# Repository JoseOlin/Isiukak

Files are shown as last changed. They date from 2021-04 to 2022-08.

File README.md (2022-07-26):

# Sistema de Conducción Isiukak

Código, piezas 3D, diagramas y esquemáticos y  para replicar el **sistema Isiukak para conducción con Joystick**.

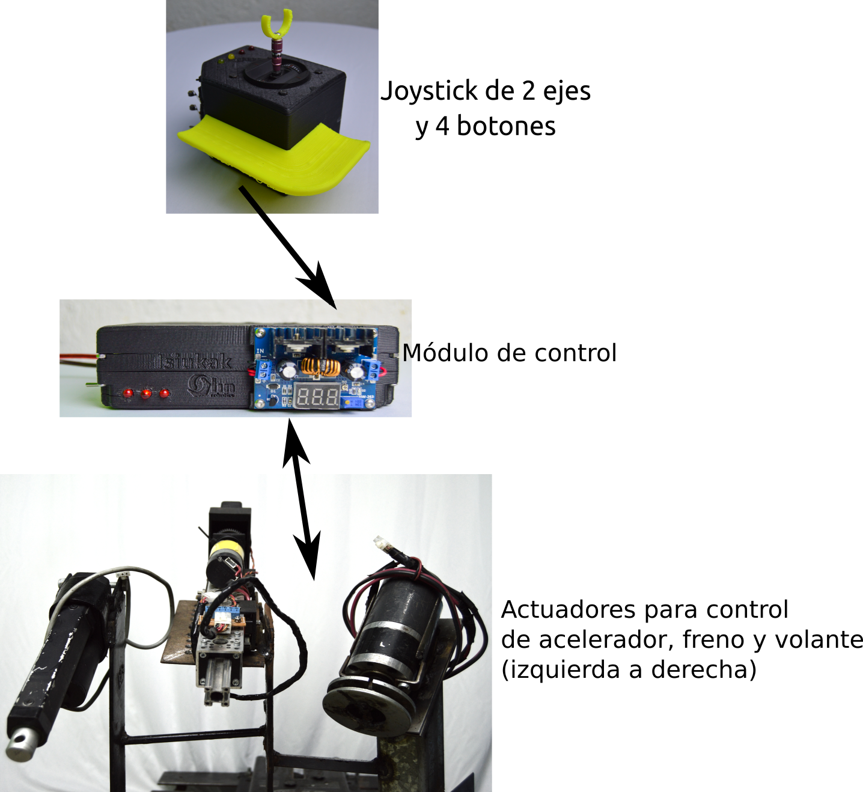
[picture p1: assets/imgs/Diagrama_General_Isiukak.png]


La carpeta **Programas** contiene dos carpetas. 
- **Arduino_PlatformIO** contiene el código en lenguaje Arduino para el microcontrolador del módulo de control. 
- **MonitorSerial_Qt** es un programa en C++/Qt para monitorear los valores del sistema en tiempo real.

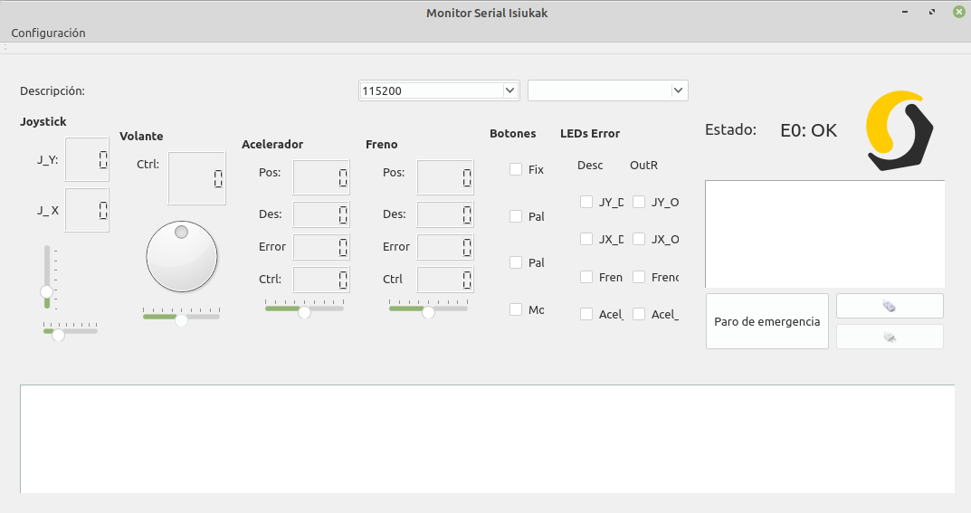
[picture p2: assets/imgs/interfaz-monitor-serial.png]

Más detalles en el [archivo README.md de la carpeta Programas](Programas/README.md)

La carpeta **Componentes_3DParts_Schematics** contiene el diagrama general del sistema y los esquemáticos de cada subsistema, así como las piezas 3D necesarias y fotografías de las piezas construidas.

Si requieres más información acerca de los componentes del sistema puedes visitar la [página del proyecto Isiukak en Olin Robotics](https://www.olinrobotics.com/proyecto_isiukak)

# Estructura general del sistema

Los subsistemas del Isiukak son:

- Módulo de control

- Joystick

- Actuación de pedales, volante y palanca

Que se muestran a continuación.



El **módulo de control** es la parte central, donde se realiza el procesamiento del sistema. Lee la  posición del *joystick* para controlar los pedales y el volante. 

El **eje vertical del joystick, controla el freno y el acelerador**, mientras que el **eje horizontal asiste en el movimiento del volante**. La palanca de cambios se  controla con dos botones ubicados en el mismo joystick.

Dos actuadores lineales controlan el freno y el acelerador, un tercer motor asiste en el movimiento del volante y otro actuador lineal asiste en el movimiento de la palanca.

Actualmente se tiene una prueba de concepto del sistema implementada en un Arduino UNO. La siguiente etapa portar el código a un microcontrolador de grado automotriz.

# Acerca del Software
Utilizamos [PlatformIO](https://platformio.org/) para la compilación del código en Arduino, con [Qt Creator](https://www.qt.io/product/development-tools) como editor.
 
El software se comparte con la mejor intención de que como comunidad desarrollemos tecnología de asistencia que nos permita una vida más autónoma, pero sin garantías. **Úsalo bajo tu propia responsabilidad**.

 Esperamos que te diviertas tanto como nosotros desarrollándolo. Que la Autonomía te acompañe.

## Versionado Semántico
Estamos en proceso de adoptar [versionado semántico (SemVer)](https://semver.org/) para la nomenclatura de las versiones liberadas.

Dada un número de versión MAYOR.MENOR.PATCH, se incrementa:
1. MAYOR cuando se hace un **cambio incompatible a la API**.
2. MENOR cuando se agrega funcionalidad compatible con versiones anteriores.
3. PATCH cuando se arreglan bugs compatibles con versiones anteriores.

Una versión MAYOR **0 indica que se está en las primeras etapas de desarrollo**, la API es inestable y puede tener muchos cambios.

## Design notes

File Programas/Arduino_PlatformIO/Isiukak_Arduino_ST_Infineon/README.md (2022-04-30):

# Sistema Conducción Joystick

El archivo principal es  **ControlActuadoresJoystick_Retro.cpp**

## Joystick

```
        ^
        |
        |
  <----------->  JyHor
        |
        |
        JyVer
```

### LEDs

| | L1 | L2 | L3 | L4 |
| ----- | --- | --- | --- | --- |
| Blkng | JyNoCentro | PotsDscn  | ActFueraRango | ActsNoMov  |
| Stdy  | AcelDscn | JyHorDscn | FrenoDscn | JyVerDescn |

## Botones

FijarPosiciónFreno

SubirPalanca

BajarPalanca

ModoCarretera

# Referencia de pines
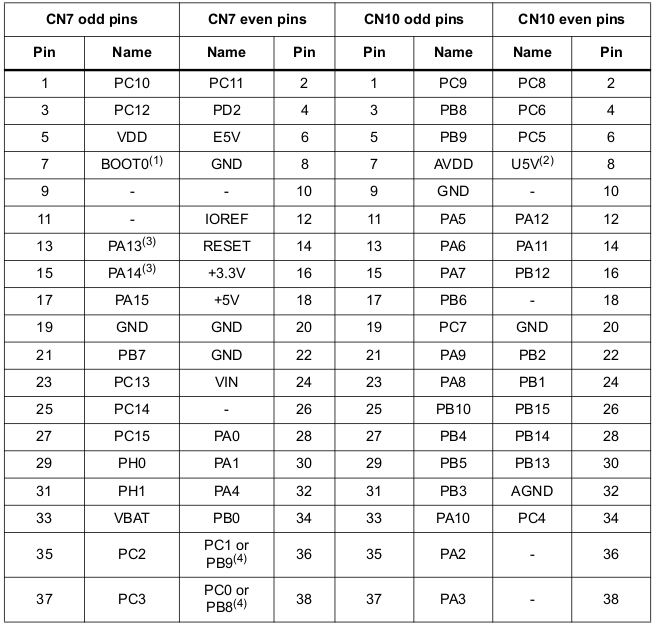
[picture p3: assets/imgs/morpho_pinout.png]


## Pines analógicos:

**A0: INPUT Analógica**. Joystick eje Y. Incremento acelera, decremento frena.

**A1: INPUT Analógica**. Josytick eje X. (Volante).

**A2: INPUT Analógica**. Pot actuador 1. (Freno).

**A3: INPUT Analógica**. Pot actuador 2. (Accel).

**A4: INPUT Digital.** (Future) J_Y second pot

**A5: INPUT Digital.** (Future) J_X second pot

En el ST NUCLEO la referencia para el ADC debe configurarse AVDD = VDDVirtual, AGND = GNDVirtual 

## Pines digitales:

### Comunicación serial con el Monitor
**0 (PA3):** Serial Rx

**1 (PA2):** Serial Tx

### Comunicación serial con los puentes
**2 (PA10): INPUT.**  **smcSerial RX**. Hacia los Drivers de los motores.

**8 (PA9): OUTPUT**. **smcSerial TX**. Hacia los Drivers de los motores.  

### Voltaje digital para corroborar conexión de potenciómetros
**3: OUTPUT**. **5V Virtual**. Para Validación de potenciómetros conectados.

**7: OUTPUT.** **GND Virtual**.

### Pines de control de la palanca
**4: OUTPUT. pinPalanca_Bajar.** Pin para controlar el puente H de la palanca.

**5: OUTPUT. pinPalanca_Bajar.** Pin para controlar el puebte H de la palanca.

### Botones y switches
**10: INPUT.** Botón Bajar Palanca.

**11: INPUT.** Switch Modo Carretera.

### Voltaje de referencia para el ADC.
**12: OUTPUT.** V_SSA Voltaje referencia ADC GND.

**13: OUTPUT**: V_DDA Volt referencia ADC VDD.

### Otros
**6**: **Not used** 

**9: INPUT_PULLUP. PinParoManualEmergencia.**

# Operation Modes

The Isiukak have 3 modes of operation.
- **Normal mode**: Read the joystick and control the actuators.
- **Embedded Testing**: Set predefined values for the joystick and the flags of connection and normal range of the pots to check if the safety routines works properly.
- **Joystick Virtual**: Pending of implementation. This mode receives remote values for the joystick over Serial.

# Calibración del Sitema

## Actuadores

Actualizar las siguientes variables:

actFreno_valorExtendido
actFreno_valorRetraido
actFreno_valorParoEmergencia

actAcel_valorExtendido
actAcel_valorRetraido

# Configurar QtCreator para compilar código de Arduino con PlatformIO

Para facilitar el desarrollo en lugar de usar el IDE de Arduino se utiliza QtCreator con PlatformIO para compilar y editar el código.

Requiere instalación de Qt Creator y PlatformIO

pip3 install -U platformio

La sección **Projects** de Qt Creator debe configurarse de la siguiente forma.

## Build Settings

Edit build configuration: Debug

**Build directory:** El directorio donde esté **platform.ini**

**Buils Steps.** Borrar todos los items

Build steps → Custom Process Step.

- Command: `platformio`
- **Arguments**: `-f -c qtcreator run`
- **Working directory**: %{buildDir}

**Clean Steps.** ``Borrar todos los items
Add clean step → Custom Process step

- **Command**: `platformio`
- **Arguments**: `-f -c qtcreator run --target clean`
- **Working directory**`: ``%{buildDir}`

## Deploy  Settings

Project → Run → Deploy configuration → Add Deploy Step → Custom Process Step
 • **Command:** platformio
 • **Arguments**: run --target upload
 • **Working directory**: %{buildDir}

# Release Notes

## 0.9.1

En esta versión el actuador del freno puede tener retroalimentación con una resistencia variable (por ejemplo con los actuadores de Pololu o Servocity) o con un encoder (por ejemplo el actuador de GoBilda)

# Tareas futuras

**TODO**: Implementar lectura de status de los drivers DC para detectar sobretemperatura, etc. P2
**TODO**: Cambiar el orden de los pines para dejar el 2 para Serial y que sea compatible con ST NUCLEO.

# Standards a Considerar

## MISRA C

Motor Industry Software Reliability Association C Standard

## AUTOSAR

## NASA (Código)

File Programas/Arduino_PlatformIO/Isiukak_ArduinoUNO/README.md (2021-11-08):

# Sistema Conducción Joystick

El archivo principal es **ControlActuadoresJoystick_Retro.cpp**

## Joystick

```
        ^
        |
        |
  <----------->  JyHor
        |
        |
        JyVer
```

### LEDs

| | L1 | L2 | L3 | L4 |
| ----- | --- | --- | --- | --- |
| Blkng | JyNoCentro | PotsDscn  | ActFueraRango | ActsNoMov  |
| Stdy  | AcelDscn | JyHorDscn | FrenoDscn | JyVerDescn |

## Botones

FijarPosiciónFreno

SubirPalanca

BajarPalanca

ModoCarretera

# Referencia de pines

## Pines analógicos:

**A0: INPUT Analógica**. Joystick eje Y. Incremento acelera, decremento frena.
**A1: INPUT Analógica**. Josytick eje X. (Volante).
**A2: INPUT Analógica**. Pot actuador 1. (Freno).
**A3: INPUT Analógica**. Pot actuador 2. (Accel).
**A4: INPUT Digital.** Botón Fijar Posición Freno
**A5: INPUT Digital.** Botón Subir Palanca.

## Pines digitales:

**15: I2C SDA**:  Conectado a A4 ó A5.
**14: I2C SCL**:  Conectado a A4 ó A5.
13: Pendiente de implementación
12: Pendiente de implementación
**11: INPUT.** Switch Modo Carretera.
**10: INPUT.** Botón Bajar Palanca.

**9: INPUT_PULLUP. PinParoManualEmergencia.**
**8: OUTPUT**. Tx Software serial. Hacia los Drivers de los motores.
**7: INPUT.** Rx Software Serial. Desde los Drivers de los motores.

6: INPUT. Implementar GND Virtual en este pin para liberar el 2 para comunicación del ST.
**5: OUTPUT. pinPalanca_Bajar.** Pin para controlar el puebte H de la palanca.
**4: OUTPUT. pinPalanca_Bajar.** Pin para controlar el puente H de la palanca.

**3: OUTPUT**. **5V Virtual**. Para Validación de potenciómetros conectados.
**2: OUTPUT**. **GND Virtual**. Para Validación de potenciómetros conectados

**1:** Serial Tx
**0:** Serial Rx

# Calibración del Sitema

## Actuadores

Actualizar las siguientes variables:

actFreno_valorExtendido
actFreno_valorRetraido
actFreno_valorParoEmergencia

actAcel_valorExtendido
actAcel_valorRetraido

# Configurar QtCreator para compilar código de Arduino con PlatformIO

Para facilitar el desarrollo en lugar de usar el IDE de Arduino se utiliza QtCreator con PlatformIO para compilar y editar el código.

Requiere instalación de Qt Creator y PlatformIO

pip3 install -U platformio

La sección **Projects** de Qt Creator debe configurarse de la siguiente forma.

## Build Settings

Edit build configuration: Debug

**Build directory:** El directorio donde esté **platform.ini**

**Buils Steps.** Borrar todos los items

Build steps → Custom Process Step.

- Command: `platformio`
- **Arguments**: `-f -c qtcreator run`
- **Working directory**: %{buildDir}

**Clean Steps.** ``Borrar todos los items
Add clean step → Custom Process step

- **Command**: `platformio`
- **Arguments**: `-f -c qtcreator run --target clean`
- **Working directory**`: ``%{buildDir}`

## Deploy  Settings

Project → Run → Deploy configuration → Add Deploy Step → Custom Process Step
 • **Command:** platformio
 • **Arguments**: run --target upload
 • **Working directory**: %{buildDir}

# Release Notes

## 0.9.1

En esta versión el actuador del freno puede tener retroalimentación con una resistencia variable (por ejemplo con los actuadores de Pololu o Servocity) o con un encoder (por ejemplo el actuador de GoBilda)

# Tareas futuras

**TODO**: Implementar lectura de status de los drivers DC para detectar sobretemperatura, etc. P2
**TODO**: Cambiar el orden de los pines para dejar el 2 para Serial y que sea compatible con ST NUCLEO.

# Standards a Considerar

## MISRA C

Motor Industry Software Reliability Association C Standard

## AUTOSAR

## NASA (Código)

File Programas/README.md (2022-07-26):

La carpeta **Arduino_(PlatformIO)** incluye el **código en lenguaje Arduino para el microcontrolador del módulo de control**. Se utiliza **PlatformIO** para compilar el código y **Qt Creator como IDE de desarrollo**.

La carpeta con el código más completo está en **Isiukak_Arduino_ST_Infineon**.

La carpeta **MonitorSerial_(Qt)** incluye el código para monitorear el sistema en tiempo real. La computadora donde se ejecute este programa (en nuestro caso una minilaptop) debe conectarse el módulo de control por USB. 

Imagen de la interfaz del monitor serie

# Instalar udev rules para tarjetas ST.
	curl -fsSL https://raw.githubusercontent.com/platformio/platformio-core/master/scripts/99-platformio-udev.rules | sudo tee /etc/udev/rules.d/99-platformio-udev.rules
	
	sudo cp /media/Ext4/Recursos/Electronica/Tarjetas_Desarrollo/ST/99-platformio-udev.rules /etc/udev/rules.d/99-platformio-udev.rules

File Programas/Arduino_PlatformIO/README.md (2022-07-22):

Hay varias versiones:
- **Isiukak_ArduinoUNO**: Recomendable sólo para probar el funcionamiento general del sistema. No se utilice para un sistema que se vaya a probar en un automóvil.
- 
- **Isiukak_Arduino_ST_Infineon**: Es la versión que se utiliza en las pruebas en el auto.

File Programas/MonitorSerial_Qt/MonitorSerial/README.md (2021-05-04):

Programa para leer los valores del Módulo de control por Comunicación Serial.

El programa separa los valores y los muestra en modo gráfico.

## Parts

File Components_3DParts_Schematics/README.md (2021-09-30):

El PDF Diagrama_y_Esquematicos_Isiukak_ArduinoV4.pdf  incluye:

- Diagrama de los componentes del módulo de control (pags. 1 y 2)

- Esquemático del Módulo de control: p. 3

- Esquemático del circuito del Joystick: p. 4

- Esquemático de los Actuadores: pags. 5 y 6

En cada carpeta hay información del subsistema en cuestión, como esquemáticos de los circuitos y versiones gráficas en Fritzing, imágenes de los circuitos construidos, las piezas 3D necesarias, así como hojas de datos e información adicional recomendada.

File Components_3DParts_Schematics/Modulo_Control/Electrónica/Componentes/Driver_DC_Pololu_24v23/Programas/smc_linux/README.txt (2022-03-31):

Pololu Simple Motor Controller Software

Release Date: 2010-11-19
http://www.pololu.com/

== Summary ==

This binary release contains the Pololu Simple Motor Control Center
(SmcCenter) and the Simple Motor Controller command-line utility
(SmcCmd).  These programs allow you to configure and control the
Simple Motor Controller over USB.

== Prerequisites ==

You will need to download and install these packages:

  libusb-1.0-0-dev mono-runtime libmono-winforms2.0-cil

In Ubuntu, you can do this with the command:

  sudo apt-get install libusb-1.0-0-dev mono-runtime libmono-winforms2.0-cil

== USB Configuration ==

You will need to copy the file 99-pololu.rules to /etc/udev/rules.d/
in order to grant permission for all users to use Pololu USB devices.
If you already plugged in a Pololu USB device, you should unplug it at
this point so the new permissions will get applied later when you plug
it back in.

== Running the programs ==

You can run the programs by typing one of the following commands:

   ./SmcCenter
   ./SmcCmd

O alternativamente: 
   $ mono ./SmcCenter

If you get an error message that says "cannot execute binary file",
then try running the program with the mono runtime, for example:

   mono ./SmcCmd

(si no encuentra la tarjeta correr con sudo)

== Source Code ==

The C# source code for SmcCmd will be available in the Pololu USB
Software Development Kit, available at:

  http://www.pololu.com/docs/0J41

== Contact Us ==

If you have any questions, please contact us by visiting:
  http://www.pololu.com/contact

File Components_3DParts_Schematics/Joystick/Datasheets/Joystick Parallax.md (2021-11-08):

    Parallax Inc.
    JOYSTICK 5K OHM 2 AXIS PNL MT
    Joystick, 2 - Axis Analog (Resistive) Output

https://www.digikey.com/product-detail/en/parallax-inc/27808/27808-ND/4700913

https://www.digikey.com/catalog/en/partgroup/gimbal-joystick-with-adapter/44274?mpart=27808&vendor=149

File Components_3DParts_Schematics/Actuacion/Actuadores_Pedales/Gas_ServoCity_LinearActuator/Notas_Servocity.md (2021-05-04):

# Actuador lineal ServoCity
https://www.servocity.com/6-stroke-25-lb-thrust-heavy-duty-linear-actuator/

## Specs

| Stroke | 6" |
| :--- | --- |
| Operating Temperature | -26°C ~ +65°C |
| Motor Type | 3 Pole Ferrite |
| Feedback Style | 10KΩ Potentiometer |
| Gear Material | Metal Gear Train, Nylon Pinion |
| Wire Length | 24" |
| Weight | 43.3 oz |
| Voltage Range (Recommended) | 6V - 12V |
| Speed (No Load)* | 2.00” per second |
| Gearbox Style | Straight Cut Spur |
| Gear Ratio | 5:1 |
| Speed (Max Load)* | 1.37” per second |
| Dynamic Thrust* | 25 lbs |
| Static Load | 500 lbs |
| Current Drain (No-Load)*  | 800mA |
| Current Drain (Max Load)* | 3.8A  |
| Current Drain (Stall)* | 15A |

## Feedback connection

Yellow -> Feedback GND 

Blue ->  Wiper, connected to Analog pin

White -> 5V

Black -> Power GND

Red -> Power VIN

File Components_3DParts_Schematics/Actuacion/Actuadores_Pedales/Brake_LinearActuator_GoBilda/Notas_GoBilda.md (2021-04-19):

Debe comprarse el motor GoBilda adicionalmente (en la misma página de ServoCity )

# GoBilda

https://www.servocity.com/5202-series-yellow-jacket-planetary-gear-motor-5-2-1-ratio-1150-rpm-3-3-5v-encoder

[5202 Series Yellow Jacket Planetary Gear Motor (5.2:1 Ratio, 1150 RPM, 3.3 - 5V Encoder)](https://www.servocity.com/5202-series-yellow-jacket-planetary-gear-motor-5-2-1-ratio-1150-rpm-3-3-5v-encoder)
$39.99

Envío: 58 USD

**Además debe comprarse el soporte del motor (el kit no lo incluye)**:

32mm Bore Bottom Tapped Clamping Mount (Part 555176)

https://www.servocity.com/32mm-bore-clamping-mount

[4-Pos JST PH [MH-FC] to 4-Pos JST XH [MH-FC] Adaptor (500mm Length)](https://www.gobilda.com/4-pos-jst-ph-mh-fc-to-4-pos-jst-xh-mh-fc-adaptor-500mm-length/)
$4.99

[SPDT Miniature Limit Switch with Roller Lever (2 pack)](https://www.servocity.com/spdt-miniature-snap-action-micro-switch-with-roller-lever)
$2.49

## Limit switches

How To Use An External Limit Switch Kit With A Linear Actuator

http://blog.actuonix.com/2018/05/how-to-use-external-limit-switch-kit.html

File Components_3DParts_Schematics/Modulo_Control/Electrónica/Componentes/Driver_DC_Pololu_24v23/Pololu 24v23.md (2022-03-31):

# Pololu Simple High-Power Motor Controller 24v23

https://www.pololu.com/product/1383

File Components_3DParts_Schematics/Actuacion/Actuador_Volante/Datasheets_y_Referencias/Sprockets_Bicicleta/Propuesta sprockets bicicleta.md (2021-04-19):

#Dimensiones Sprocket
Díametro:
5.8cm   (14 dientes, 14t)
8.3cm   (19 dientes, 19t)

Relación: 1.431

#Motor adecuado según Información General Conducción

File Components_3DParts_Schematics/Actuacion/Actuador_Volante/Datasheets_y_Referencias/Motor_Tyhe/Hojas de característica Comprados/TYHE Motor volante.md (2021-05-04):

12V, 10A rated,

TJX60RZ-271

XZ1202

2019 09 s18

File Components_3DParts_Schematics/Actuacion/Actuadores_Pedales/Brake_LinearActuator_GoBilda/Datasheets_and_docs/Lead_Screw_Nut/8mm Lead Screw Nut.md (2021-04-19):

3505 Series Lead Screw Pattern Nut (8mm Lead, 4 Start, 32mm OD, 16mm Length)

SKU: 3505-0804-3216

https://www.servocity.com/8mm-lead-screw-nut-0-770-pattern/

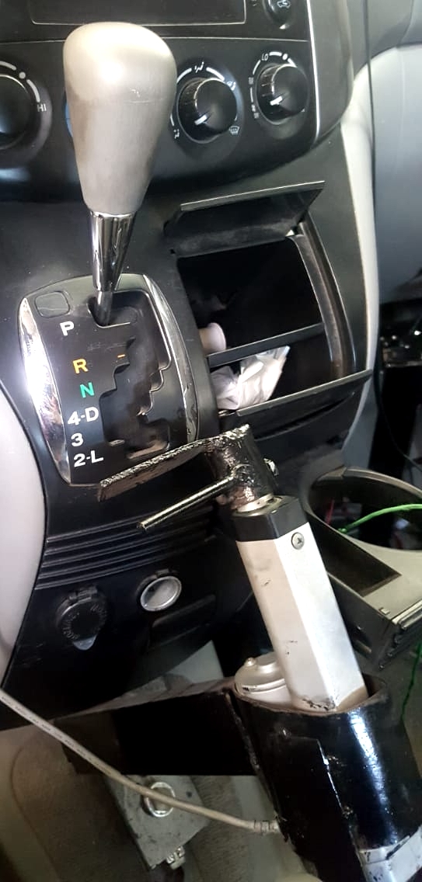
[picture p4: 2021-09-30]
Components_3DParts_Schematics/Actuacion/Actuador_Palanca/Images/b20b28bb-8cbb-4feb-86f6-bfede2309cf5.jpeg

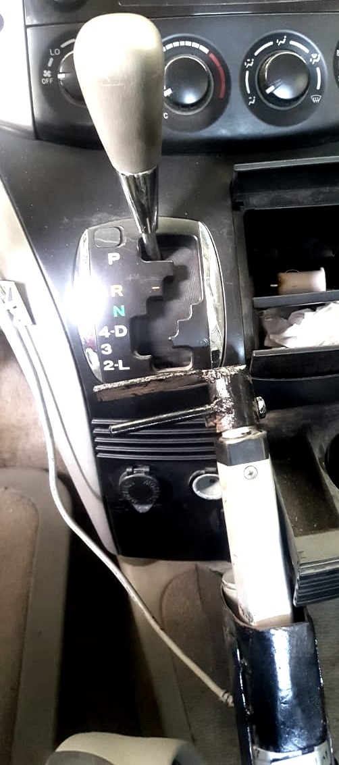
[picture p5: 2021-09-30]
Components_3DParts_Schematics/Actuacion/Actuador_Palanca/Images/8d8ab2b0-adf1-464f-bf73-c042a085edb0.jpeg

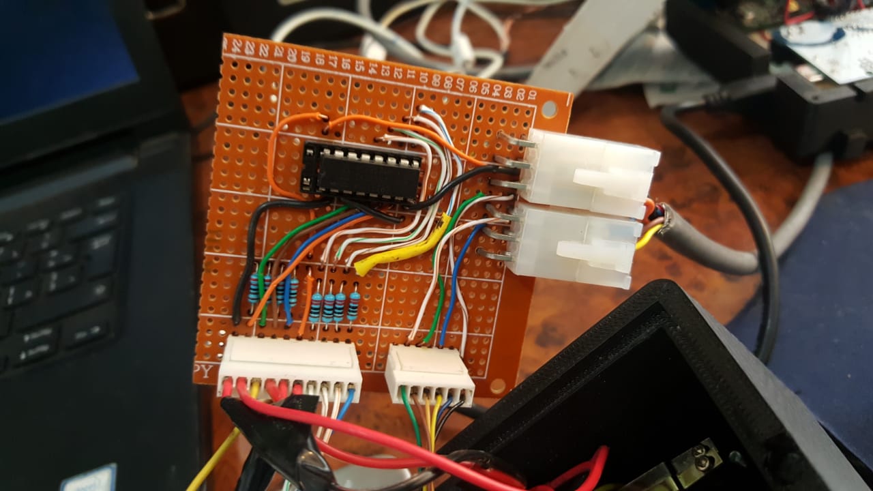
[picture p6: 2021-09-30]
Components_3DParts_Schematics/Joystick/Images/Joystick_Circuito_Foto.jpeg

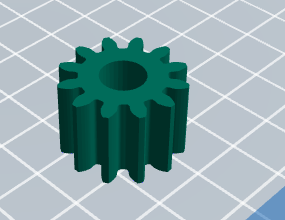
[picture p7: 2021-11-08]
Components_3DParts_Schematics/Actuacion/Actuadores_Pedales/Brake_LinearActuator_GoBilda/3D_Parts/Feedback_Pot_Parts/Feedback_Gears/Engrane_15mm_12dientes.png

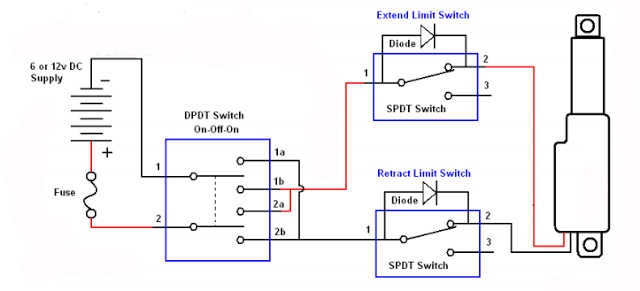
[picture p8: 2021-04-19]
Components_3DParts_Schematics/Actuacion/Actuadores_Pedales/Brake_LinearActuator_GoBilda/Datasheets_and_docs/Actuator End limit switches.jpg

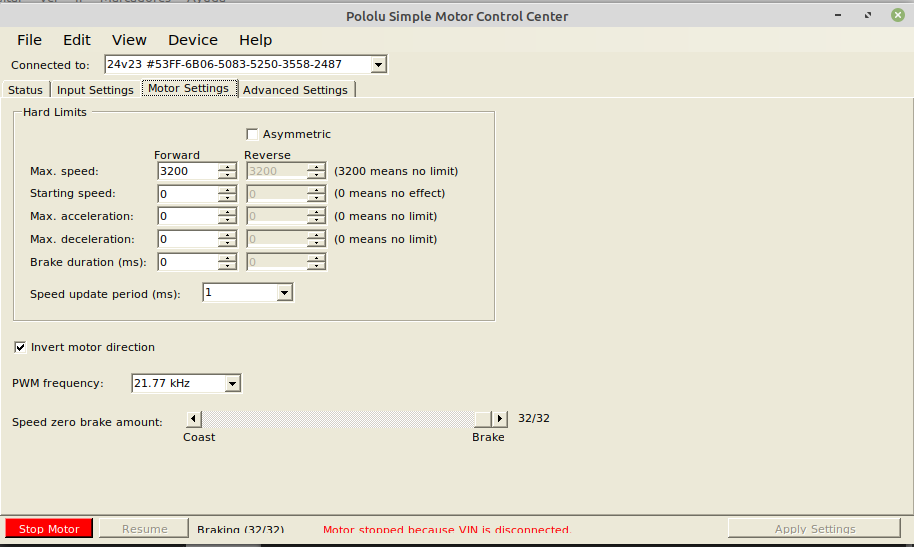
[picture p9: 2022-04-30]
Components_3DParts_Schematics/Modulo_Control/Electrónica/Componentes/Driver_DC_Pololu_24v23/Imagenes/ConfigDrivers/ksnip_20220428-195205.png

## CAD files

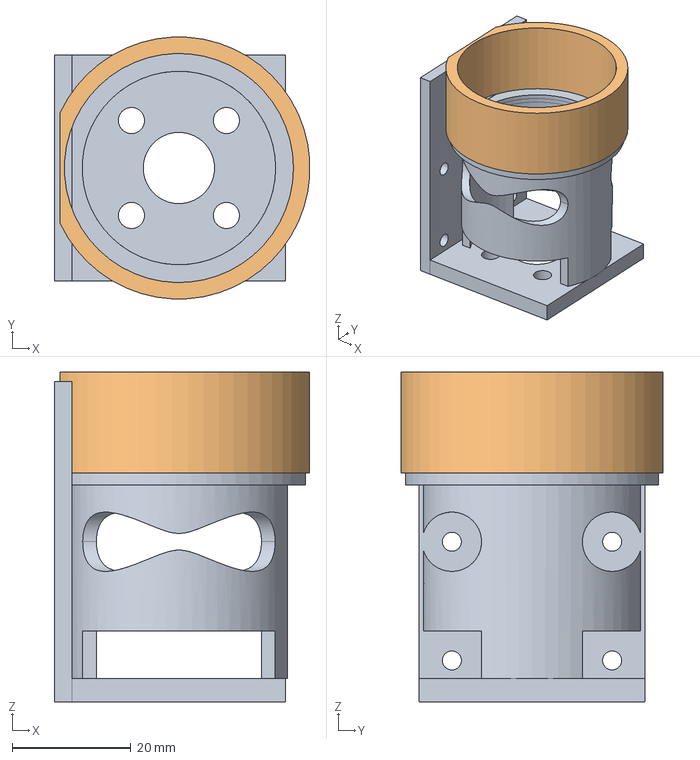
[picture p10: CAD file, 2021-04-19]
Components_3DParts_Schematics/Actuacion/Actuadores_Pedales/Brake_LinearActuator_GoBilda/3D_Parts/SoporteMotor/SoporteMotor_v4_Ensamble/SoporteMotor_Ensamble.FCStd
43.0 x 44.1 x 55.6 mm
SoporteAngularMotor_001
SoporteAngularMotor_CilindroMotor_001

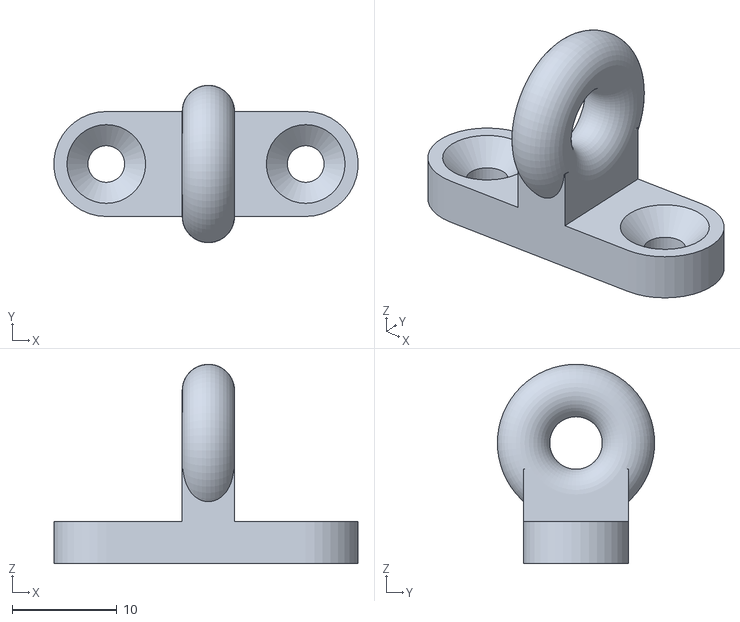
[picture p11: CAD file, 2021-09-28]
Components_3DParts_Schematics/Actuacion/Actuador_Palanca/Piezas_3D/Guia cable.STL
29.0 x 15.0 x 19.0

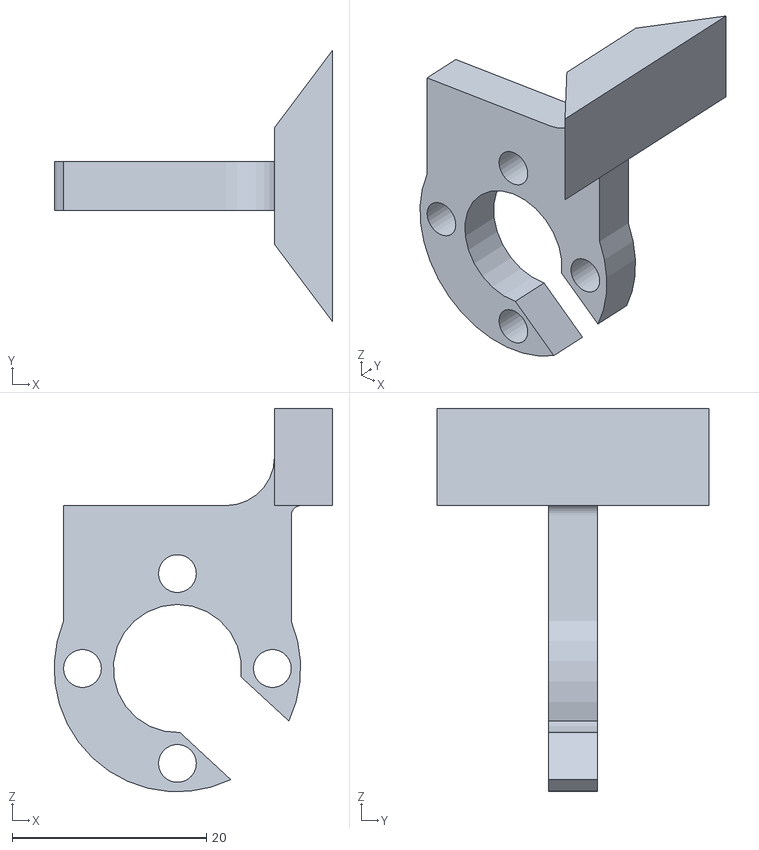
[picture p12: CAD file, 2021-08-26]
Components_3DParts_Schematics/Actuacion/Actuadores_Pedales/Brake_LinearActuator_GoBilda/3D_Parts/ActivadorLimitSwitch/ActivadorLimitSwitch_v4.stl
28.7 x 28.0 x 39.4

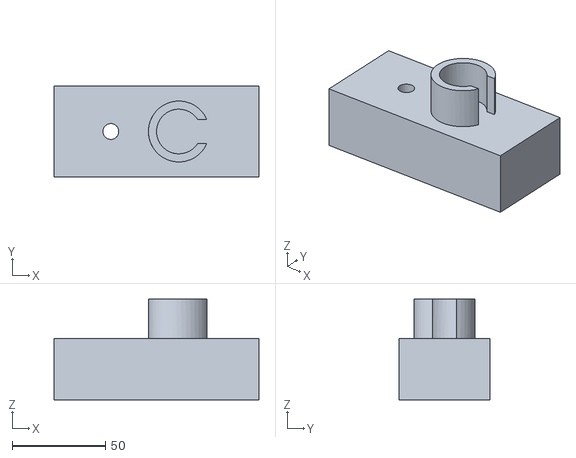
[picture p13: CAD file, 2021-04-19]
Components_3DParts_Schematics/Actuacion/Actuadores_Pedales/Brake_LinearActuator_GoBilda/3D_Parts/Feedback_Pot_Parts/CajaEngranes_Feedback/Caja para engranes v1.stl
110.0 x 49.0 x 54.0

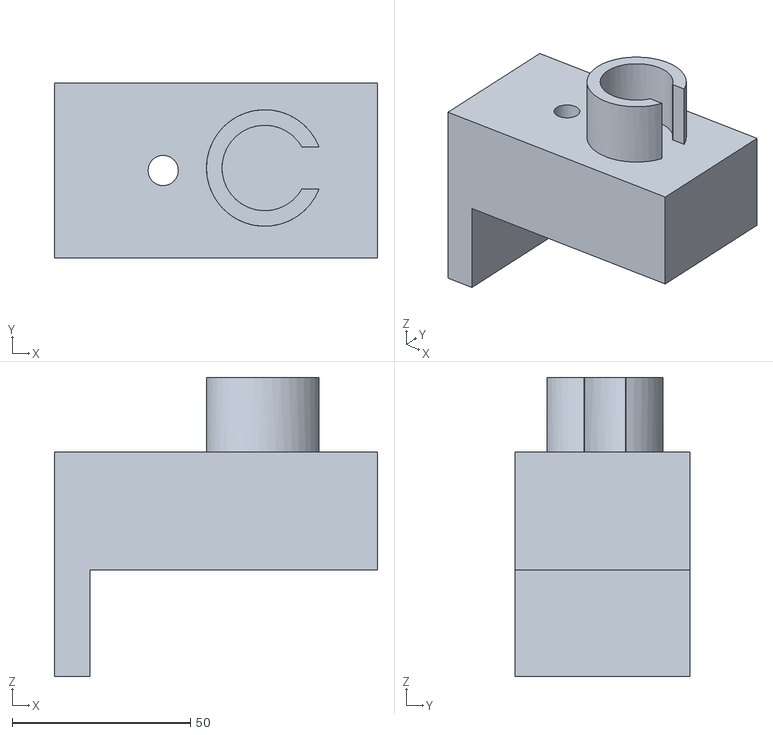
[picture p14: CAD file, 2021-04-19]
Components_3DParts_Schematics/Actuacion/Actuadores_Pedales/Brake_LinearActuator_GoBilda/3D_Parts/Feedback_Pot_Parts/CajaEngranes_Feedback/V2/Caja para engranes v2.stl
90.6 x 49.0 x 84.0

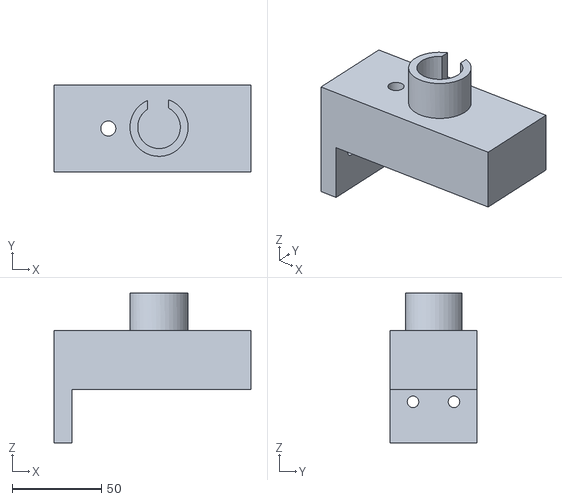
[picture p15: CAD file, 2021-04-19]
Components_3DParts_Schematics/Actuacion/Actuadores_Pedales/Brake_LinearActuator_GoBilda/3D_Parts/Feedback_Pot_Parts/CajaEngranes_Feedback/V3_2020_09/Caja para engranes v3.stl
110.6 x 49.0 x 84.0

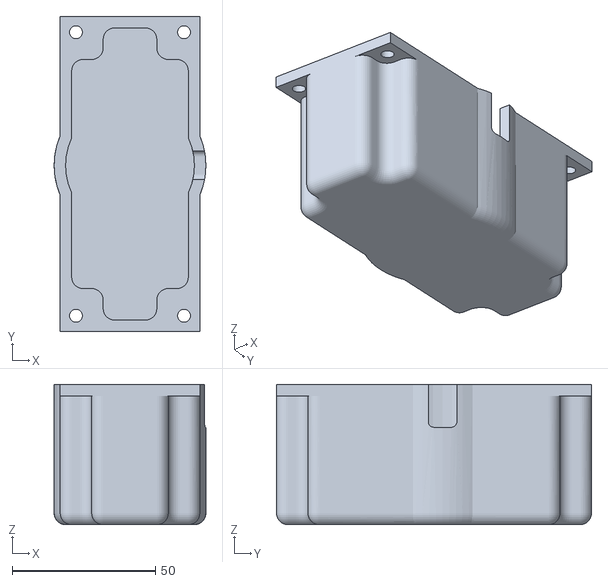
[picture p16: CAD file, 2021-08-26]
Components_3DParts_Schematics/Actuacion/Actuadores_Pedales/Brake_LinearActuator_GoBilda/3D_Parts/Feedback_Pot_Parts/CubiertaEngranesRetro/CubiertaEngranes.STL
53.0 x 110.0 x 49.0

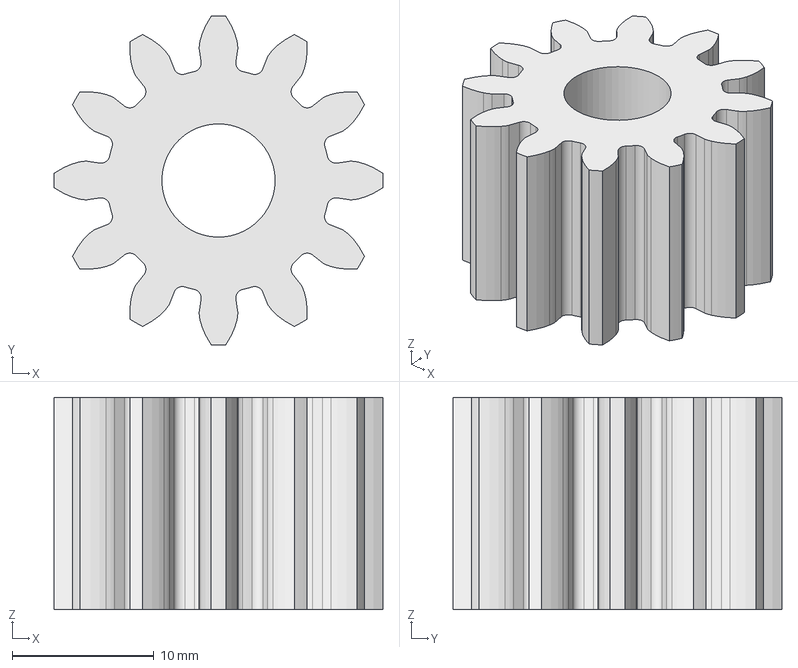
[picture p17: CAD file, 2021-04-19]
Components_3DParts_Schematics/Actuacion/Actuadores_Pedales/Brake_LinearActuator_GoBilda/3D_Parts/Feedback_Pot_Parts/Feedback_Gears/Engranje 15mm 12 dientes 1.66.FCStd
23.2 x 23.2 x 15.0 mm

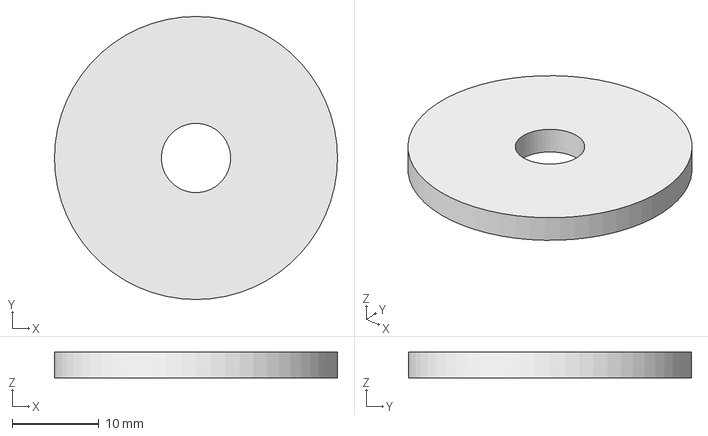
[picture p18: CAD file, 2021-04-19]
Components_3DParts_Schematics/Actuacion/Actuadores_Pedales/Brake_LinearActuator_GoBilda/3D_Parts/Feedback_Pot_Parts/Tapa potenciometro.FCStd
32.7 x 32.7 x 3.00 mm

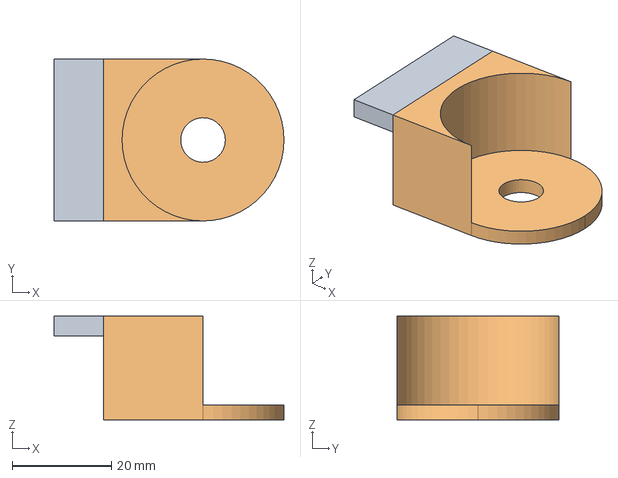
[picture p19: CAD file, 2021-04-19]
Components_3DParts_Schematics/Actuacion/Actuadores_Pedales/Brake_LinearActuator_GoBilda/3D_Parts/Feedback_Pot_Parts/Tapa_Soporte_Potenciometro/Tapa con soporte para Potenciometro.FCStd
46.4 x 32.7 x 21.0 mm

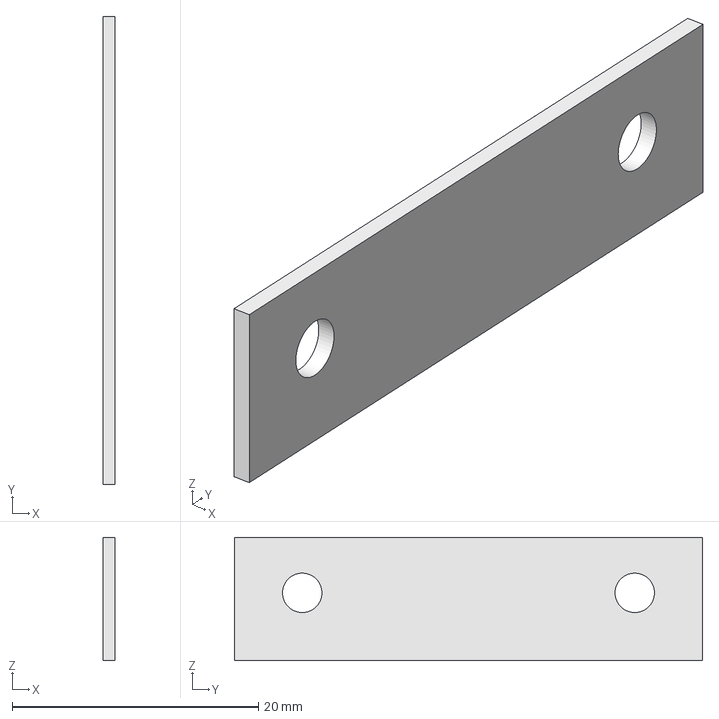
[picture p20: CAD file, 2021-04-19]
Components_3DParts_Schematics/Actuacion/Actuadores_Pedales/Brake_LinearActuator_GoBilda/3D_Parts/SoporteMotor/Separador/SeparadorAjuste_Motor.fcstd
1.00 x 38.0 x 10.0 mm

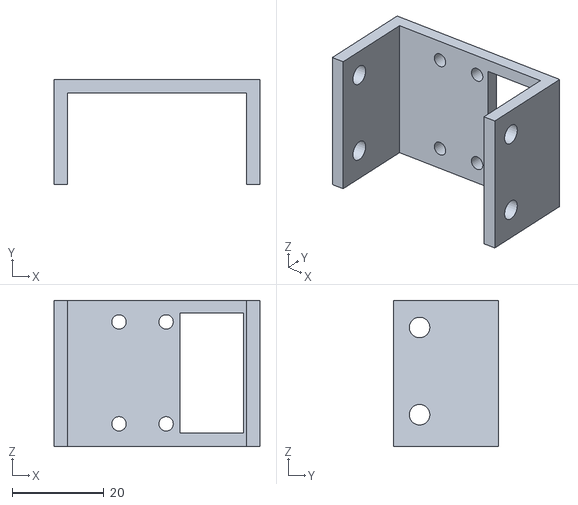
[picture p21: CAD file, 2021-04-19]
Components_3DParts_Schematics/Actuacion/Actuadores_Pedales/Brake_LinearActuator_GoBilda/3D_Parts/SoporteSwitch/SoporteSwitch_v4.stl
45.0 x 23.0 x 32.0

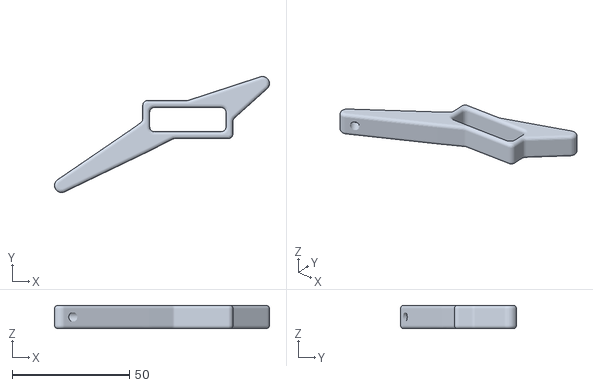
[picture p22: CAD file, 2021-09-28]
Components_3DParts_Schematics/Adicionales/Piezas_3D/Palanca_llave_Toyota_V2.STL
91.7 x 49.5 x 10.0

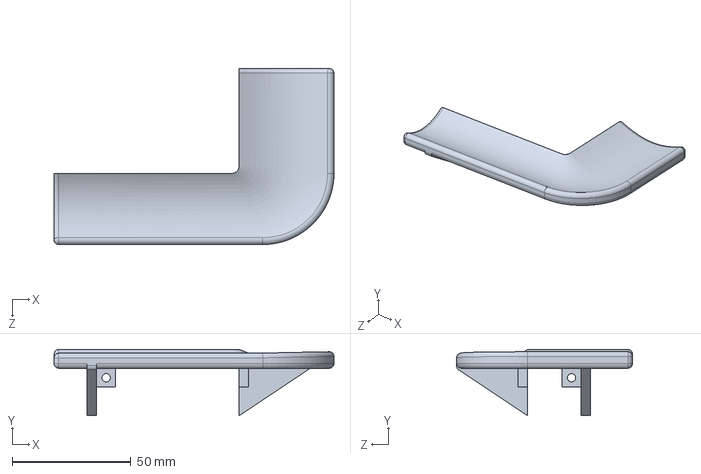
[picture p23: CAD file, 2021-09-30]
Components_3DParts_Schematics/Joystick/Piezas_3D/Reposa-Mano.SLDPRT
118.0 x 28.0 x 74.2 mm

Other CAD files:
Components_3DParts_Schematics/Actuacion/Actuadores_Pedales/Brake_LinearActuator_GoBilda/3D_Parts/SoporteMotor/SoporteMotor_v5/SoporteMotor_Ensamble.FCStd
Components_3DParts_Schematics/Modulo_Control/Piezas_3D/tapa base final 2.SLDPRT
Components_3DParts_Schematics/Actuacion/Actuadores_Pedales/Brake_LinearActuator_GoBilda/3D_Parts/ActivadorLimitSwitch/ActivadorLimitSwitch.FCStd
Components_3DParts_Schematics/Actuacion/Actuadores_Pedales/Brake_LinearActuator_GoBilda/3D_Parts/Feedback_Pot_Parts/CajaEngranes_Feedback/Caja para engranes 1.FCStd
Components_3DParts_Schematics/Actuacion/Actuadores_Pedales/Brake_LinearActuator_GoBilda/3D_Parts/Feedback_Pot_Parts/CajaEngranes_Feedback/V2/Caja para engranes 1 (1).FCStd
Components_3DParts_Schematics/Actuacion/Actuadores_Pedales/Brake_LinearActuator_GoBilda/3D_Parts/Feedback_Pot_Parts/CajaEngranes_Feedback/V3_2020_09/Caja para engranes 1.FCStd
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

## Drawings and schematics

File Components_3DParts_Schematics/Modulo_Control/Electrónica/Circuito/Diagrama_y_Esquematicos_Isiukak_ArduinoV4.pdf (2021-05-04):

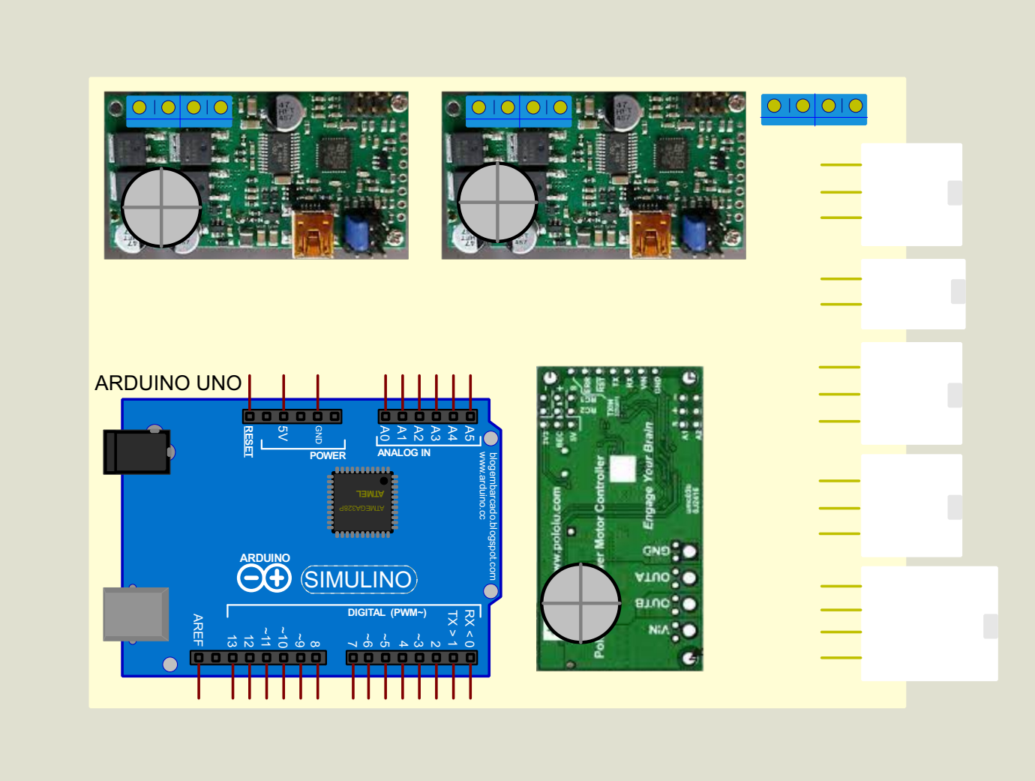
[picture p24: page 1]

w .arduino.cc blogembarcado.blogspot.com

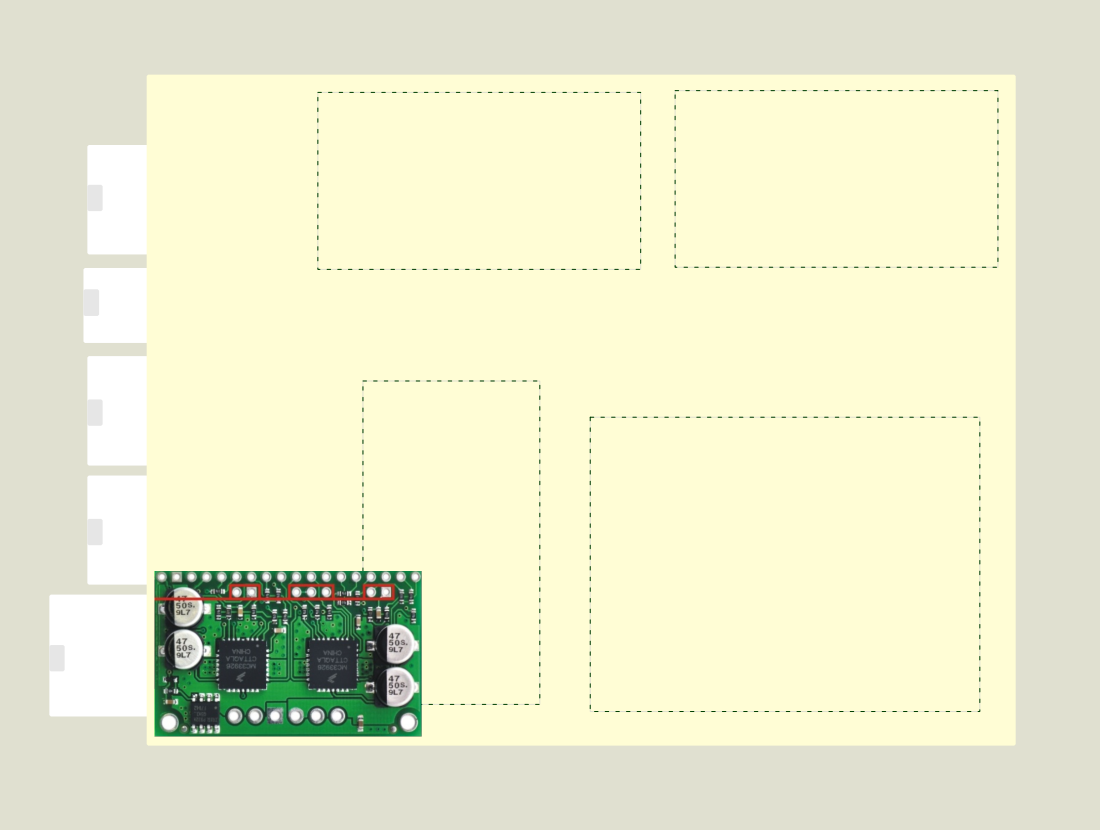
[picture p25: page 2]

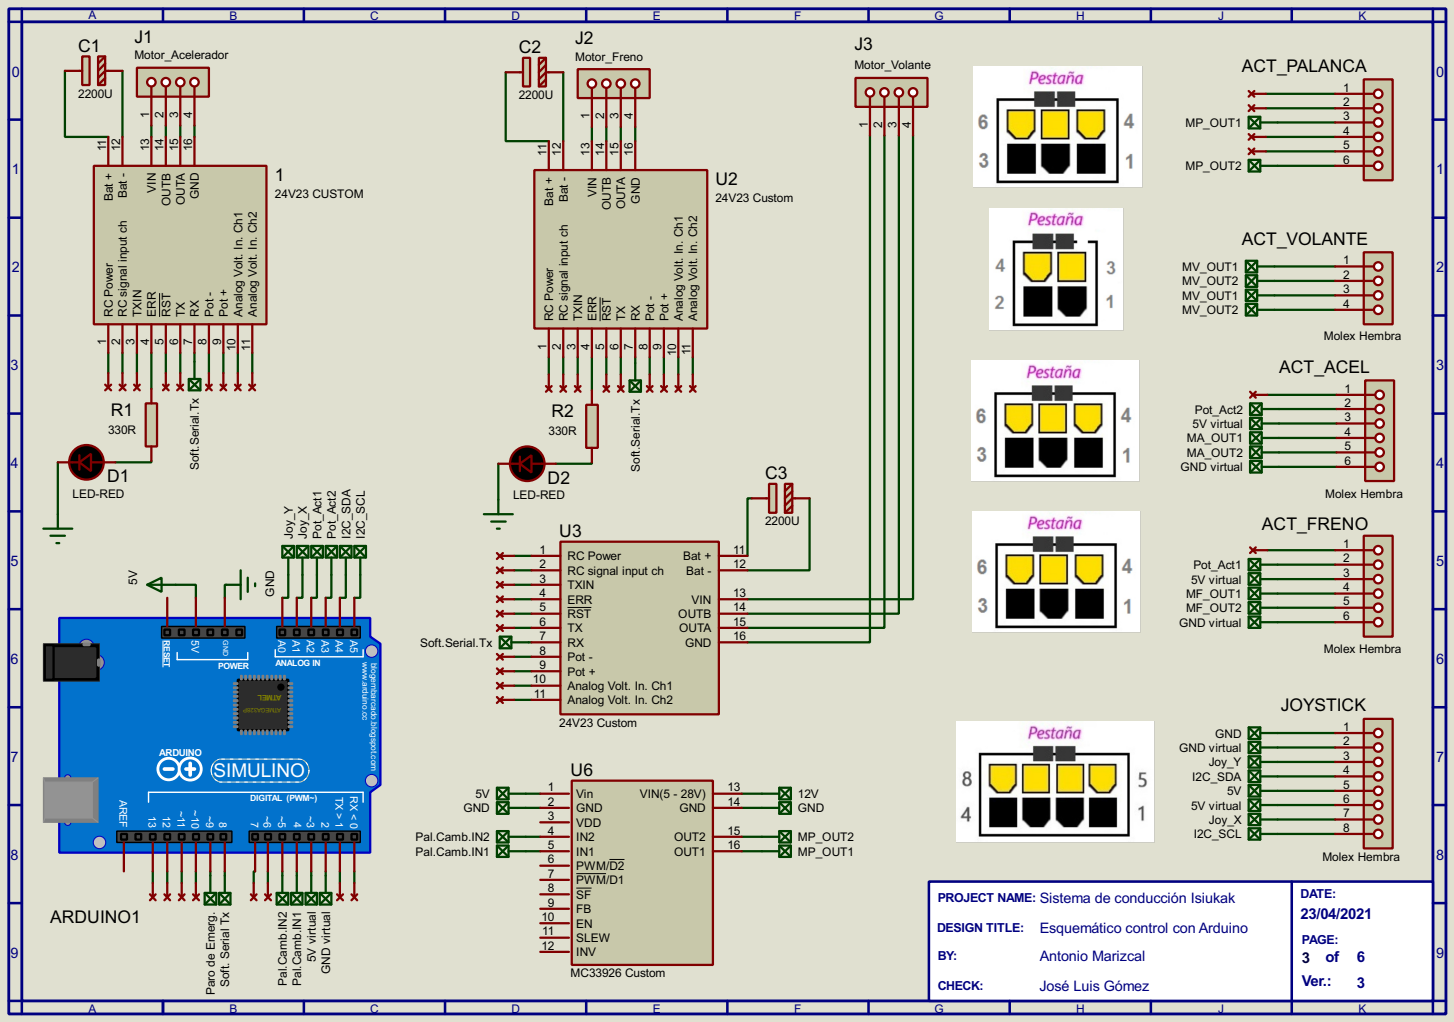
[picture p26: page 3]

11 RC signal input ch

7 Pot - 8 Analog Volt. In. Ch1

Soft. Serial Tx Paro de Emerg. Soft.Serial.Tx

Joy_Y GND virtual 5V virtual Pal.Camb.IN1 Pal.Camb.IN2

w .arduino.cc blogembarcado.blogspot.com

Pal.Camb.IN2 Pal.Camb.IN1

Sistema de conducción Isiukak

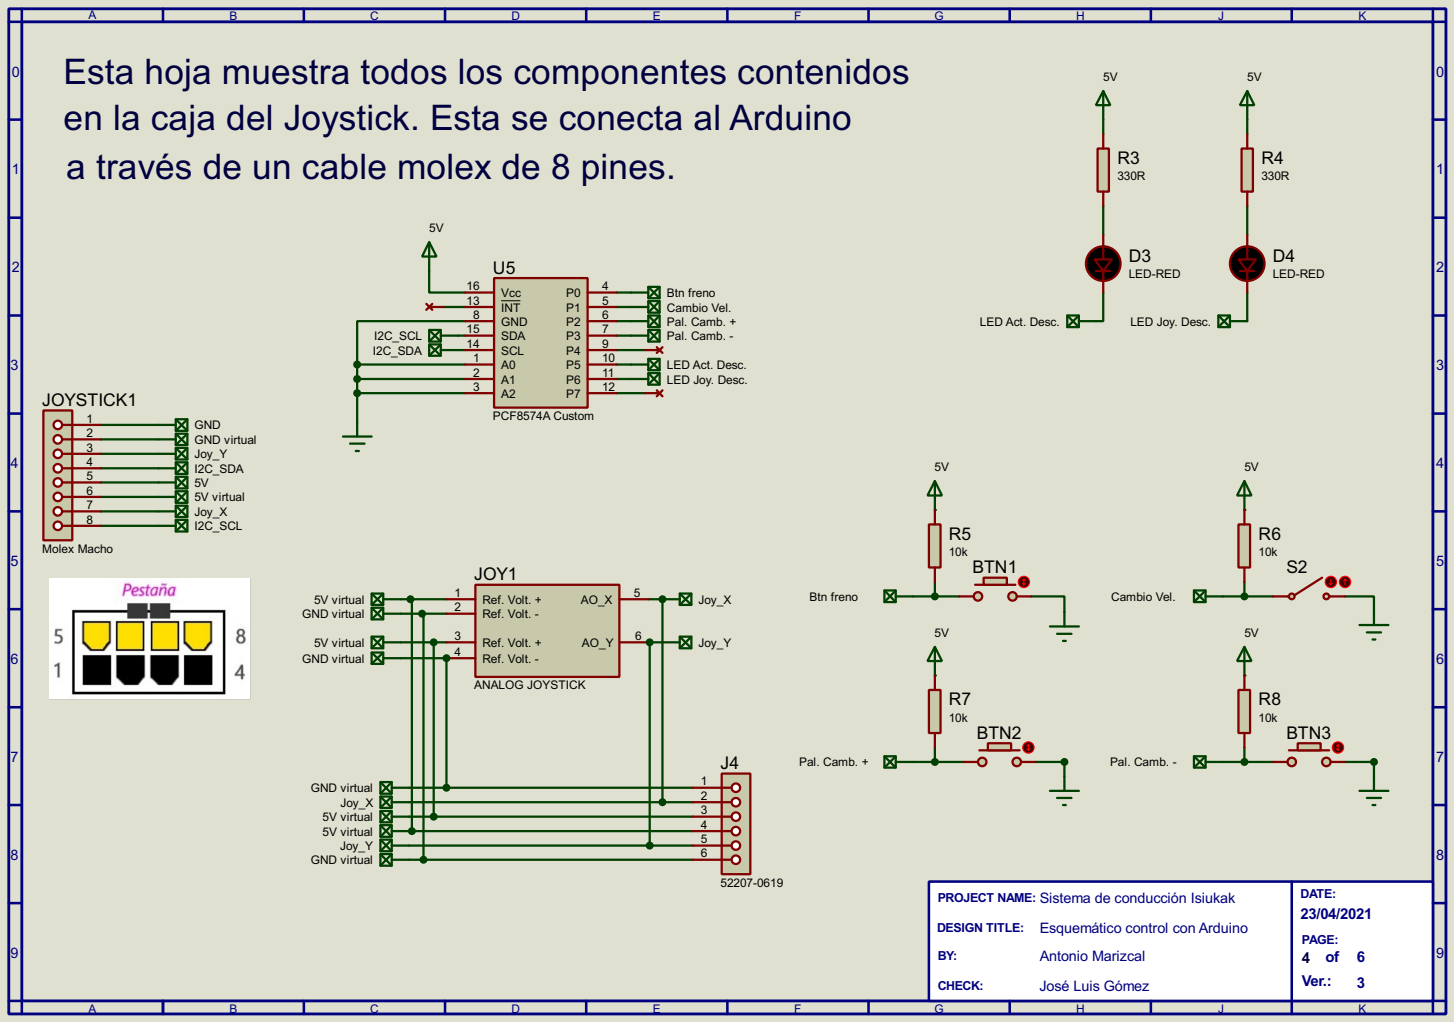
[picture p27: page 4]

Esta hoja muestra todos los componentes contenidos
en la caja del Joystick. Esta se conecta al Arduino
a través de un cable molex de 8 pines.

Btn freno Cambio Vel. Pal. Camb. + Pal. Camb. - LED Act. Desc. LED Joy. Desc.

5V virtual 5V virtual Joy_Y GND virtual

Sistema de conducción Isiukak

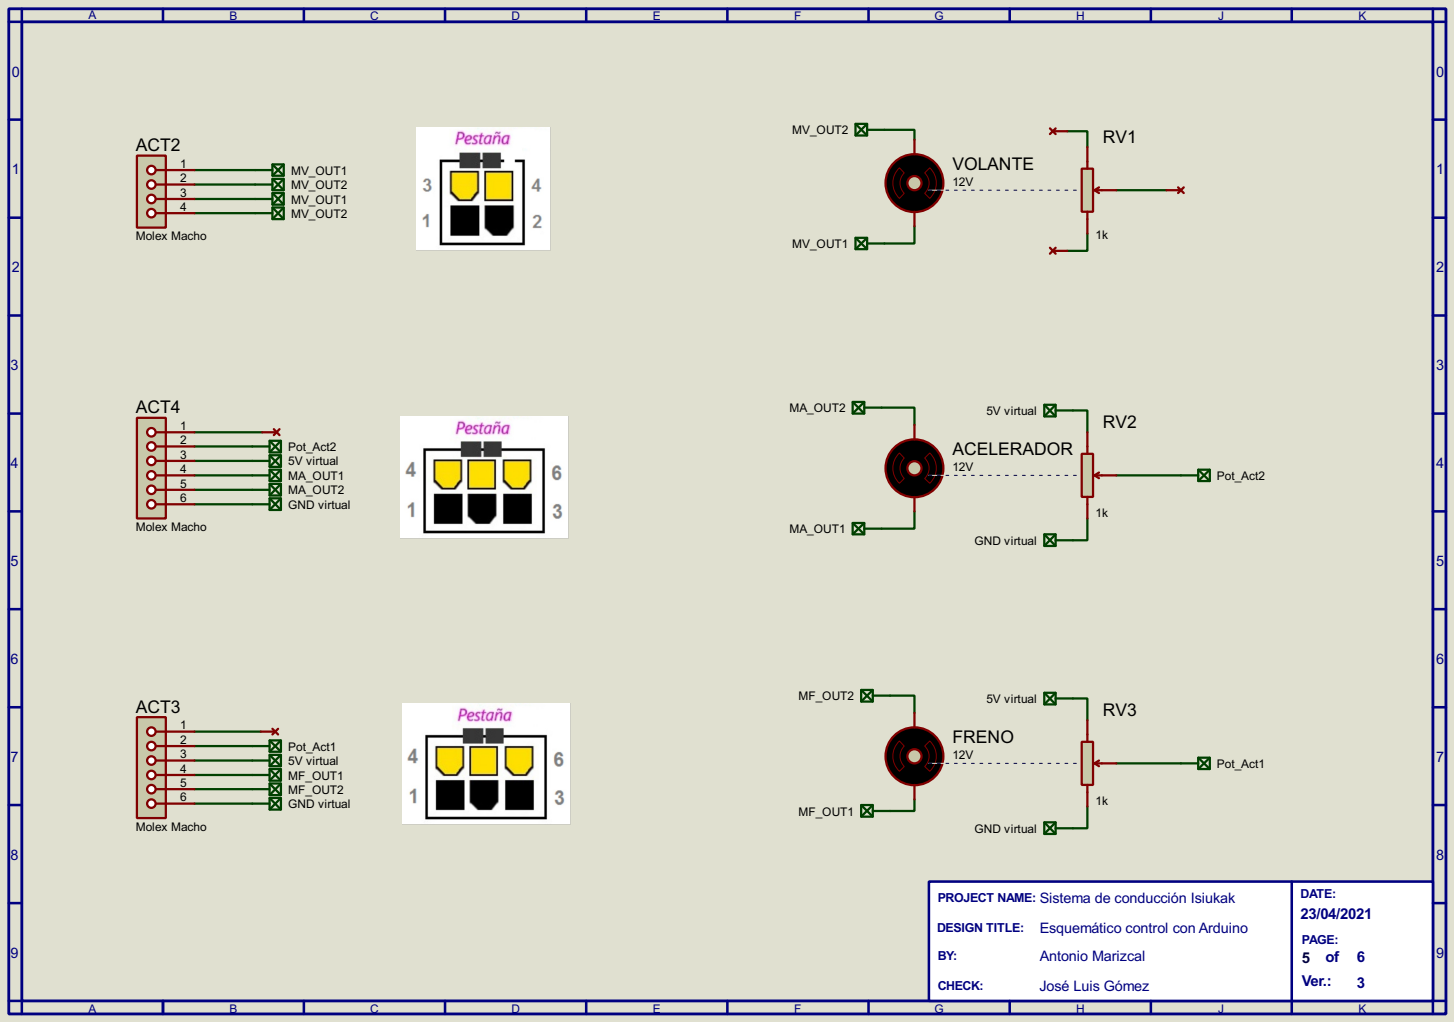
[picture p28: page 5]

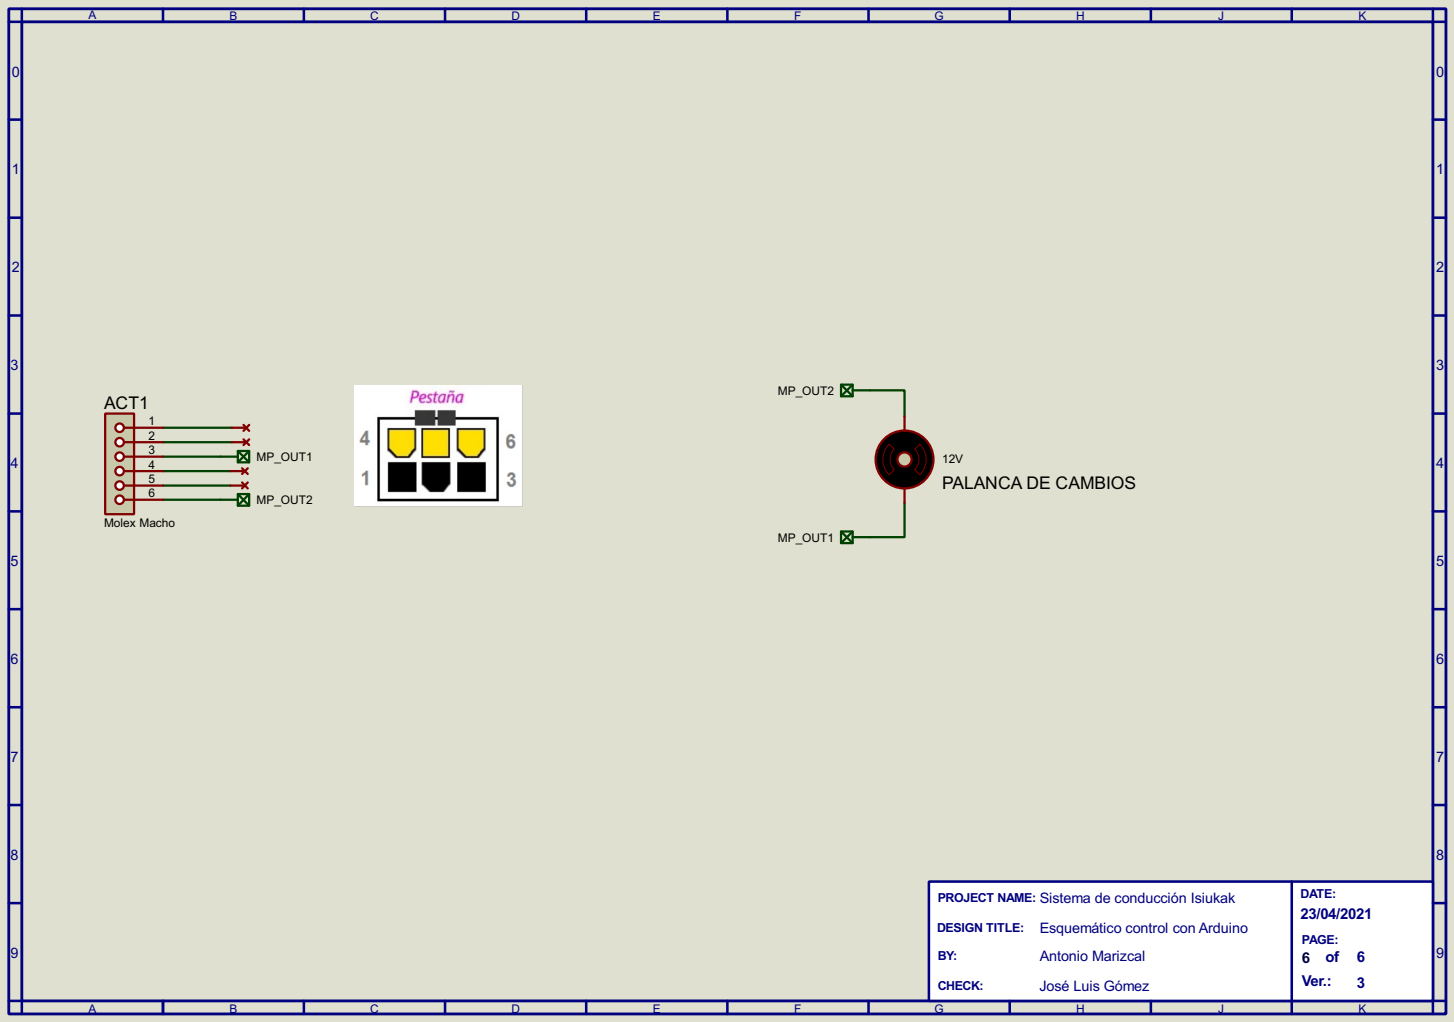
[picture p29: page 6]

Sistema de conducción Isiukak

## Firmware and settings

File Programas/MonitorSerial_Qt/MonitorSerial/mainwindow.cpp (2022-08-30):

/* Programa para leer el puerto serie del arduino del Sistema de Conducción
 *
 *
 *
 *
 */

#include "mainwindow.h"


//QString serialPort;
int baudRate = QSerialPort::Baud115200;
//int baudRate = QSerialPort::Baud9600;
//int baudRate = QSerialPort::Baud38400;


QString cadJoystickActivado = "J_ac";
QString cadJx_Desc = "J_x_Desc";
QString cadJy_Desc = "J_y_Desc";
QString cadJx_OutOfRange = "J_x_OutOfRange";
QString cadJy_OutOfRange = "J_y_OutOfRange";

QString cadAcelActivado = "A_ac";
QString cadAcelInhibido = "A_inh";
QString cadAcel_Desc = "Acel_Desc";
QString cadAcel_OutOfRange = "Acel_OutOfRange";

QString cadAccel_VIN = "A_Vin";
QString cadAccel_Temp = "A_Tmp";
QString cadAccel_Error = "A_Err";

QString cadBrakeActivado = "B_ac";
QString cadBrakeInhibido = "B_inh";
QString cadBrakeDesc = "Freno_Desc";
QString cadBrake_OutOfRange = "Brake_OutOfRange";

QString PotError_header = "EPot_";
QString cadBrake_VIN = "B_Vin";
QString cadBrake_Temp = "B_Tmp";
QString cadBrake_Error = "B_Err";

QString cadVolanteActivado = "V_ac";
QString cadVolanteModo = "V_m";
QString cadVolanteControl = "Vol_c";
QString cadSteer_VIN = "V_Vin";
QString cadSteer_Temp = "V_Tmp";
QString cadSteer_Error = "V_Err";

QString cadPalancaActivada = "Shft_a";

QString cadEstadoSistema = "edo";
QString cadT = "T";
QString cadNormalDefines = "nDef";

QString cadTemp_uC = "Tm_uC";
QString cadTemp_Therm1 = "Tm_Th1";
QString cadTemp_Therm2 = "Tm_Th2";

QString cadCompsReconnected = "Componentes Reconectados y en Rango Válido";
QString cadParoEmergenciaManual = "Paro de Emergencia Manual.";
QString cadRestartTesting = "Testing";




vector<driverValuesRow> brake_driverMat; //Used for testing purposes.

// Usadas en desplegarValores(QString renglonDatos)


MainWindow::MainWindow(QWidget *parent) : QMainWindow(parent), ui(new Ui::MainWindow)
{
    ui->setupUi(this);


    ////// Inicialización y llenado de los elementos
    // Comunicación serial.
    serial = new QSerialPort(this);

    //buscarPuertos();

    fillPortsInfo();
    fillPortsParameters();


    /// Conexiones.
    connect(serial,     SIGNAL(readyRead()),
            this,       SLOT(readData())          );

    connect(ui->cmbSerialPortSelector,  SIGNAL(currentIndexChanged(int)),
           this,                       SLOT(showPortInfo(int))   );


    int joyY_Center = 510;
    int joyY_MinVal = joyY_Center - 130;
    int joyY_MaxVal = joyY_Center + 130;
    //int joyY_FrenoCambios = 600;

    // ** Eje X (Volante)
    int joyX_Center = 512;  //
    int joyX_MinVal = joyX_Center - 130;  //
    int joyX_MaxVal = joyX_Center + 130;  //

    ui->joystickVertical_sld->setMinimum(joyY_MinVal);
    ui->joystickVertical_sld->setMaximum(joyY_MaxVal);
    ui->joystickHorizontal_Sld->setMinimum(joyX_MinVal);
    ui->joystickHorizontal_Sld->setMaximum(joyX_MaxVal);


    ui->btnConectar->click(); //Conectar automáticamente al arranque.

    // Initialize gridLayout with 5 rows of empty labels, plus the headers row.
    uint rows = 5;
    uint cols = 12; //Vin, Temp and 10 possible errors.
    for (uint row = 0; row < rows; row++)
    {
        //vector<QLabel*> rowQLabels;
        //erroresMatrix_lbl.push_back(rowQLabels);
        for (uint col = 0; col < cols; col++)
        {
            QLabel* lbl = new QLabel();
            lbl->setText("0");
            //erroresMatrix_lbl[row].push_back(lbl);

            //ui->driverErrorsValues_gridLayout->addWidget(lbl, row, col, 1, 1, Qt::AlignCenter);
            ui->driverErrorsHeaders_gridLayout->addWidget(lbl, row + 1, col, 1, 1, Qt::AlignCenter);
        }
    }

    ///////////////////////////////////////////////////

    //escena = new QGraphicsScene(0,0, 250,250);
    //ui->joystick_graphics->setScene(escena);
    qDbg << "       Inicio sesión Logging" << QDate::currentDate() << ", " << QTime::currentTime();
    qWarning() << "Prueba warning";
    qInfo() << "Prueba Info";
}

MainWindow::~MainWindow()
{
    ui->btnDesconectar->click();
    delete ui;
}


void MainWindow::desplegarValores(QString renglonDatos)
{
    /* Función para desplegar los datos que se reciben por Serial y mostrar los errores
     * en la GUI.
     * Se invoca en readData()     */

    ui->InfoSalida_txt->insertPlainText(renglonDatos);

    ui->InfoSalida_txt->ensureCursorVisible();
    ui->erroresSalida_txt->ensureCursorVisible();
    ui->driversValues_txt->ensureCursorVisible();


    /// Separar renglón datos para mostrar valores del Joystick.

    ///* Joystick
    displayInfoJoystick(renglonDatos);

    ///* Buttons
    displayInfoButtons(renglonDatos);

    ///* Brake INFO
    displayInfoBrake(renglonDatos);

    ///* Accelerator INFO
    displayInfoAccel(renglonDatos);

    ///* Steer Wheel
    displayInfoSteer(renglonDatos);

    ///* Shift gear
    displayInfoShiftGear(renglonDatos);

    ///* System status
    displaySystemInfo(renglonDatos);

    ///* Temperature values
    displayTemperature(renglonDatos);

    ///* Test restarting string when running embedded Testing
    bool testingRestartingReceived = buscarExpresionRegular("(\\*\\*)(" + cadRestartTesting + ")(\\*\\*)", renglonDatos);
    if(testingRestartingReceived)
    {
        apagarLEDsError();
    }


    ///* Errors
    QRegularExpression expRegInt_R = QRegularExpression ("(\\*\\*)(.+)(\\*\\*)");
    // \\*\\* = **             (.+) = Any character one or more times
    QRegularExpressionMatch match = expRegInt_R.match(renglonDatos);
    QString Error_s = match.captured(0);
    if( Error_s.length() > 0 )
    {
        ui->erroresSalida_txt->insertPlainText(Error_s);
        ui->erroresSalida_txt->insertPlainText("\n");
    }

}

void MainWindow::on_btnParoEmergencia_clicked()
{
    /*vector<int> rows;

    for (int i = 1; i < 9; ++i)
    {
        int sizeR = rows.size();

        if(sizeR > 4)
        {
            rows.at(0) = i;
            //rotate(rows.begin(), rows.end()-1, rows.end());
            rotate(rows.begin(), rows.begin()+1, rows.end());
            //rotate(rows.end(), rows.begin()+1, rows.begin());
            //rows.at(rows.size()-1) = i;
        }
        else {
            rows.push_back(i);
        }


        // Display current values of row.
        QString debugString;
        for (vector<int>::iterator it = rows.begin(); it != rows.end(); ++it)
        {
            debugString += QString::number(*it);
            //qDbg << ", " << *it;
        }
        //qDbg << "\n";
        qDbg << debugString;
    }
    */

    driverValuesRow brake_row;

    for(int i = 0; i < 10; i++)
    {
        qDbg << "it: " << i ;
        brake_row.Vin = 12.4 + i;
        brake_row.Temperature = 38.4 + i;

        uint16_t errorRaw = i;
        //QStringList active_errors_list;
        decodeDriverError(errorRaw, brake_row);

        //brake_row.errorsList = active_errors_list;


        /*int brake_mat_size = brake_driverMat.size();
        if(brake_mat_size > 4)
        {
            brake_driverMat.at(0) = brake_row;
            rotate(brake_driverMat.begin(),
                   brake_driverMat.begin()+1,
                   brake_driverMat.end());
        }
        else
        {
            brake_driverMat.push_back(brake_row);
        }
        */
        driverMatrixValues_insert(brake_driverMat, brake_row);


        /*for(vector<driverValuesRow>::iterator it = brake_driverMat.begin();
             it != brake_driverMat.end();
             ++it )
        {
            QString debugString;
            driverValuesRow row = *it;

            debugString += QString::number(row.Vin) + ", ";
            debugString += QString::number(row.Temperature) + ", ";

            QStringList errors = row.errorsList;
            foreach(QString error, errors)
            {
                debugString += error + ", ";
            }
            qDbg << debugString << "\n";


            //qDbg << ", " << *it;
        }
        */
        QString brakeMatString = driverMatrixErrors_display(brake_driverMat);
        //driverMatrixErrors_gridLayoutDisplay(ui->driverErrorsValues_gridLayout, brake_driverMat);
        driverMatrixErrors_gridLayoutDisplay(ui->driverErrorsHeaders_gridLayout, brake_driverMat);
        qDbg << brakeMatString;
        ui->driversValues_txt->setPlainText(brakeMatString);
    }


}
void MainWindow::driverMatrixValues_insert(vector<driverValuesRow>& driverMatrix,
                                          driverValuesRow row)
{
    int mat_size = driverMatrix.size();

    if(mat_size > 4)
    {
        driverMatrix.at(0) = row;
        rotate(driverMatrix.begin(),
               driverMatrix.begin()+1,
               driverMatrix.end());
    }
    else
    {
        driverMatrix.push_back(row);
    }
}

void MainWindow::driverMatrixValues_gridLayoutDisplay(QGridLayout* grid,
                                                      vector<driverValuesRow> driverMatrix)
{
    //TODO: C. Optimizar considerando que la matrix puede tener menos de 5 renglones.
    int row = 1; // The first row is for the headers.
    for(vector<driverValuesRow>::iterator it = driverMatrix.begin();
         it != driverMatrix.end();
         ++it )
    {
        driverValuesRow DriverRow = *it;

        QLayoutItem* gridItem = grid->itemAtPosition(row, 0);
        QLabel* gridLbl = (QLabel*)gridItem->widget();
        gridLbl->setText(QString::number(DriverRow.Vin));

        gridItem = grid->itemAtPosition(row, 1);
        gridLbl = (QLabel*)gridItem->widget();
        gridLbl->setText(QString::number(DriverRow.Temperature));

        for(int col = 2; col < 12; col++)
        {
            QLayoutItem* gridItem = grid->itemAtPosition(row, col);
            QLabel* gridLbl = (QLabel*)gridItem->widget();
            gridLbl->setText(QString::number(DriverRow.errorsArray[col]));
        }
        row++;
    }
}
void MainWindow::driverMatrixErrors_gridLayoutDisplay(QGridLayout* grid,
                                                      vector<driverValuesRow> driverMatrix)
{
    //TODO: C. Optimizar considerando que la matrix puede tener menos de 5 renglones.
    int row = 1; // The first row is for the headers.
    for(vector<driverValuesRow>::iterator it = driverMatrix.begin();
         it != driverMatrix.end();
         ++it )
    {
        driverValuesRow DriverRow = *it;


        for(int col = 0; col < 9; col++)
        {
            QLayoutItem* gridItem = grid->itemAtPosition(row, col);
            QLabel* gridLbl = (QLabel*)gridItem->widget();
            gridLbl->setText(QString::number(DriverRow.errorsArray[col]));
        }
        row++;
    }
}

QString MainWindow::driverMatrixErrors_display(vector<driverValuesRow> driverMatrix)
{

    QString matrixString;

    for(vector<driverValuesRow>::iterator it = driverMatrix.begin();
         it != driverMatrix.end();
         ++it )
    {
        QString rowString;
        driverValuesRow row = *it;

        //rowString += QString::number(row.Vin) + ", ";
        //rowString += QString::number(row.Temperature) + ", ";


        /*QStringList errors = row.errorsList;
        foreach(QString error, errors)
        {
            rowString += error + ", ";
        }*/
        //qDbg << rowString << "\n";
        //rowString += "Errors: ";

        for(int ind = 0; ind < 10; ind++)
        {
            rowString += QString::number(row.errorsArray[ind]) + ", ";
        }

        matrixString += rowString + '\n';
        //qDbg << ", " << *it;
    }
    return matrixString;
}

QString MainWindow::driverMatrixValues_display(vector<driverValuesRow> driverMatrix)
{

    QString matrixString;

    for(vector<driverValuesRow>::iterator it = driverMatrix.begin();
         it != driverMatrix.end();
         ++it )
    {
        QString rowString;
        driverValuesRow row = *it;

        rowString += QString::number(row.Vin) + ", ";
        rowString += QString::number(row.Temperature) + ", ";


        /*QStringList errors = row.errorsList;
        foreach(QString error, errors)
        {
            rowString += error + ", ";
        }*/
        //qDbg << rowString << "\n";
        rowString += "Er: ";
        for(int ind = 0; ind < 10; ind++)
        {
            rowString += QString::number(row.errorsArray[ind]) + ", ";
        }

        matrixString += rowString + '\n';
        //qDbg << ", " << *it;
    }
    return matrixString;
}

bool MainWindow::buscarExpresionRegular_findNextInt(QString expReg, QString fuente, int& match_int)
{

    //QRegularExpression expRegInt_R("J_Y: (\\d+)");

    QRegularExpression RegExp(expReg);
    QRegularExpressionMatch RegExpMatch = RegExp.match(fuente);
    //int indiceJy_Fin
    //int indiceJy_Ini = expRegInt.indexIn(renglonDatos_s);
    if(RegExpMatch.hasMatch() )
    {
        QString match_s = RegExpMatch.captured(1);
        //int match_int = match_s.toInt();
        match_int = match_s.toInt();
        return true;
    }
    else
    {
        return false;
    }
}

bool MainWindow::buscarExpresionRegular_findNextFloat(QString cadHead, QString fuente, float &match_float)
{
    QString expReg = cadHead + ": (-?(\\d+)*(\\.(\\d+))?)";
    QRegularExpression RegExp(expReg);
    QRegularExpressionMatch RegExpMatch = RegExp.match(fuente);
    //int indiceJy_Fin
    //int indiceJy_Ini = expRegInt.indexIn(renglonDatos_s);
    if(RegExpMatch.hasMatch() )
    {
        QString match_s = RegExpMatch.captured(1);
        //int match_int = match_s.toInt();
        match_float = match_s.toFloat();
        return true;
    }
    else
    {
        return false;
    }
}

bool MainWindow::buscarExpresionRegular_PotError(QString fuente, QString& matchString, int& match_int)
{
    // **EPot_I_L: V**"
    // Donde:
    // I: Índice del pot de 0 a 3.
    // L: Puede ser "L" o "H".
    // V: Valor del pot con índice N (Entero positivo).
    QString RegExpTarget = "(\\*\\*" + PotError_header + ")(.+)(\\*\\*)";
    QRegularExpression RegExp(RegExpTarget);
    QRegularExpressionMatch RegExpMatch = RegExp.match(fuente);
    if(RegExpMatch.hasMatch() )
    {
       matchString = RegExpMatch.captured(0);
       /// TODO: B. Definir el índice del pot y ponerlo en la sección correspondiente.
       return true;
    }
    return false;
}

bool MainWindow::buscarExpresionRegular(QString expReg_str, QString fuente)
{
    QRegularExpression expReg(expReg_str);
    QRegularExpressionMatch RegExMatch = expReg.match(fuente);
    if(RegExMatch.hasMatch())
    {
        return true;
    }
    else
    {
        return false;
    }

}


void MainWindow::decodeDriverError(const uint16_t errorRaw, driverValuesRow& row)
{
    /*The motor can only be driven when this register has a value of 0. (See Section 3.4 for error descriptions.)
    • Bit 0: Safe Start Violation
    • Bit 1: Required Channel Invalid
    • Bit 2: Serial Error
    • Bit 3: Command Timeout
    • Bit 4: Limit/Kill Switch
    • Bit 5: Low VIN
    • Bit 6: High VIN
    • Bit 7: Over Temperature
    • Bit 8: Motor Driver Error
    • Bit 9: ERR Line High
    • Bits 10-15: reserved */

    QStringList errorsLst = {
            "0SfStrtV",
            "1ReqChIv",
            "2SerlErr",
            "3ComTmOt",
            "4LimSwch",
            "5LowVin",
            "6HighVin",
            "7OverTmp",
            "8MDrvErr",
            "9ErrLinH"  };


    for(uint8_t bit = 0; bit < 10; bit++) // 0 to 9.
    {
        //qDbg << "bit: " << bit;
        uint16_t mask = pow(2, bit);
        //qDbg << "mask: " << mask;

        uint16_t errorBit = errorRaw & mask;
        if(errorBit)
        {
            row.errorsArray[bit] = 1;

            QString errorDesc = errorsLst[bit];
            //qDbg << errorDesc;
            row.errorsList.append(errorDesc);
        }
        else{
            row.errorsArray[bit] = 0;
        }
    }
}

bool MainWindow::Limits_update(int currentValue,    int& min,        int& max,
                                                    QLabel* min_lbl, QLabel* max_lbl)
{
    if(currentValue < 0 || currentValue > 1023)
    {
        return false;
    }
    else
    {
        if( currentValue < min )
        {
            min = currentValue;
            min_lbl->setText(QString::number(min));
        }

        if( currentValue > max )
        {
            max = currentValue;
            max_lbl->setText(QString::number(max));
        }
    }
    return true;
}

void MainWindow::displayInfoJoystick(QString renglonDatos)
{
    //** Joystick Y
    bool jy_Received = buscarExpresionRegular_findNextInt("J_Y: (\\d+)", renglonDatos, valorJy);

    if(jy_Received)
    {
        ui->joystick_Y_lcd->display(valorJy);
        ui->joystickVertical_sld->setValue(valorJy);

        bool limitsValid_Jy = Limits_update(valorJy,    Joy_Y_min,      Joy_Y_max,
                                                        ui->Jy_Min_lbl, ui->Jy_Max_lbl);
        if(!limitsValid_Jy)
        {
            QString msg = "J_y. Valor rcv fuera de valores lógicos (0, 1023)";
            ui->erroresSalida_txt->insertPlainText(msg);
            ui->erroresSalida_txt->insertPlainText(renglonDatos);

            qDebug() << msg;
            qDebug() << "Renglón datos: " << renglonDatos;
        }
    }

    //** Joystick X
    bool Jx_received = buscarExpresionRegular_findNextInt("J_X: (\\d+)", renglonDatos, valorJx);
    if(Jx_received)
    {
        ui->joystick_X_lcd->display(valorJx);
        ui->joystickHorizontal_Sld->setValue(valorJx);

        bool limitsValid_Jx = Limits_update(valorJx,    Joy_X_min,      Joy_X_max,
                                                        ui->Jx_Min_lbl, ui->Jx_Max_lbl);
        if(!limitsValid_Jx)
        {
            ui->erroresSalida_txt->insertPlainText(QString("J_x. Valor rcv fuera de valores lógicos (0, 1023)"));
            ui->erroresSalida_txt->insertPlainText(renglonDatos);
        }
    }

    //** Activado
    bool statusJoystickActivado_Received =
            buscarExpresionRegular_findNextInt(cadJoystickActivado+ ": (-?(\\d+))",
                                         renglonDatos, Joystick_Activado);
    //if(statusJoystickActivado_Received)
    //{
        checkBoxBouncing(ui->joystick_Activado_chk, statusJoystickActivado_Received);
        checkBoxColor(ui->joystick_Activado_chk);
    //}

    //** Desconectado
    QString cadJyDescFull = "(\\*\\*)(" + cadJy_Desc + ")(\\*\\*)";
    bool LED_Joystick_Y_Desconectado = buscarExpresionRegular(cadJyDescFull, renglonDatos);
    checkBoxBouncing_Errors(ui->chk_LED_Joy_Y_Desc, LED_Joystick_Y_Desconectado);
    checkBoxColor_Error(ui->chk_LED_Joy_Y_Desc);

    bool LED_Joystick_X_Desconectado = buscarExpresionRegular("(\\*\\*)(" + cadJx_Desc + ")(\\*\\*)", renglonDatos);
    checkBoxBouncing_Errors(ui->chk_LED_Joy_X_Desc, LED_Joystick_X_Desconectado);
    checkBoxColor_Error(ui->chk_LED_Joy_X_Desc);

    //** OutOfRange
    bool LED_Joystick_Y_OutOfRange = buscarExpresionRegular("(\\*\\*)(" + cadJy_OutOfRange + ")(\\*\\*)", renglonDatos);
    checkBoxBouncing_Errors(ui->chk_LED_Joy_Y_OutR, LED_Joystick_Y_OutOfRange);
    checkBoxColor_Error(ui->chk_LED_Joy_Y_OutR);

    bool LED_Joystick_X_OutOfRange = buscarExpresionRegular("(\\*\\*)(" + cadJx_OutOfRange + ")(\\*\\*)", renglonDatos);
    checkBoxBouncing_Errors(ui->chk_LED_Joy_X_OutR, LED_Joystick_X_OutOfRange);
    checkBoxColor_Error(ui->chk_LED_Joy_X_OutR);

}
void MainWindow::displayInfoButtons(QString renglonDatos)
{
    /// Fix Brake Position.
    buscarExpresionRegular_findNextInt("bFB: (-?(\\d+))",
                                        renglonDatos, statusFixFreno);
    checkBoxBouncing(ui->FixFreno_chk, statusFixFreno);

    /// Modo Carretera
    buscarExpresionRegular_findNextInt("bMC: (-?(\\d+))",
                                        renglonDatos, statusModoCarr);
    checkBoxBouncing(ui->RoadMode_chk, statusModoCarr );

    buscarExpresionRegular_findNextInt("bPU: (-?(\\d+))",
                                         renglonDatos, statusPalancaUp);
    checkBoxBouncing(ui->PalUp_chk, statusPalancaUp);

    buscarExpresionRegular_findNextInt("bPD: (-?(\\d+))",
                                         renglonDatos, statusPalancaDown);
    checkBoxBouncing(ui->PalDown_chk, statusPalancaDown);
}
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

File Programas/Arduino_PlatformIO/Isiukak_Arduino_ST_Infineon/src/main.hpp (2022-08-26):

#ifndef MAIN_HPP
#define MAIN_HPP

#include "Seguridad.hpp"
#include "Testing.hpp"

//Variables para la medición del periodo del sistema.
long tiempoAnterior = 0, tiempoActual = 0;

uint8_t actualizacionExitosa = false;
//******************************************************************************//

bool validateDefinesNormalUse()
{
    definesNormalUse = true;
    //assert(JOYSTICK_ACTIVADO);

    // Checking defines that must be activated
    uint8_t mustBeActivated[13] = {
        JOYSTICK_ACTIVADO,
        FRENO_ACTIVADO,
        ACELERADOR_ACTIVADO,
        VOLANTE_ACTIVADO,
        PALANCA_ACTIVADA,

        INFO_JOYSTICK,
        INFO_BOTONES,
        INFO_ACTUADORES_POS,
        INFO_ACTUADORES_CONTROL,
        INFO_VOLANTE,
        INFO_PALANCA,

        INFO_MOTOR_DRIVERS,
        INFO_TIME
    };

    uint8_t mustBeDeactivated[7] = {
        JOYSTICK_VIRTUAL,
        TESTING_EMBEDDED,
        TESTING_FUNCTIONS,

        ENTRADAS_VIRTUALES,
        VERIFICACION_ADC,
        DEBUG_BOOT,
        DEBUG_POTS_VALUES,
        //DEBUG_POTS_ERROR_VALUES
    };

    uint activatedsArrayLenght  = sizeof(mustBeActivated);
    for(uint cont = 0; cont < activatedsArrayLenght; cont++)
    {
        if(!mustBeActivated[cont])
        {
            definesNormalUse = false;
            Serial.print("**Element ");
            Serial.print(cont);
            Serial.println(" of MustBeActivated Array is deactivated**");
        }
    }

    uint deactivatedsArrayLenght  = sizeof(mustBeDeactivated);
    for(uint cont = 0; cont < deactivatedsArrayLenght; cont++)
    {
        if(mustBeDeactivated[cont])
        {
            definesNormalUse = false;
            Serial.print("**Element ");
            Serial.print(cont);
            Serial.println(" of MustBeDeactivated Array is Activated**");
        }
    }


    if(timeOutSetted > timeOut) {
        definesNormalUse = false;
        Serial.println("**TimeOut Setted > TimeOut Target on smcSerial.**");
    }

    return definesNormalUse;
}



void Control(int Joystick_X, int Joystick_Y,
                uint8_t ActuadorFreno_EstaInhibido,
                uint8_t ActuadorAcelerador_EstaInhibido,
                TiposControlVolante tipoControlVolante)
{
    /*!
     *****************************************************************************************/

    // *************  *************** //

    ControlarPedales(Joystick_Y, FijarPosicionFreno, Joystick_comportamientoDirecto,
                     ActuadorFreno_EstaInhibido, ActuadorAcelerador_EstaInhibido);


    ControlarVolante(Joystick_X, tipoControlVolante);


    ControlPalanca(ActuadorFreno_Posicion);
}

void setUnusedPins_input_pullDown()
{
#if NUCLEO_F40
    /*STM32 datasheet recommends to set all unused pins
     * to reduce consumption
    As input with pull-up or pull-down resistor or
    As output if EM noise is an issue for the application.*/

    pinMode(pinD6, INPUT_PULLDOWN);
    /*
    pinMode(PB_13, INPUT_PULLDOWN); //MORPHO_CN10_30
    pinMode(PB_14, INPUT_PULLDOWN); //MORPHO_CN10_28
    pinMode(PB_15, INPUT_PULLDOWN); //MORPHO_CN10_26
    pinMode(PB_1, INPUT_PULLDOWN); //MORPHO_CN10_24
    pinMode(PB_2, INPUT_PULLDOWN); //MORPHO_CN10_22
    pinMode(PB_12, INPUT_PULLDOWN); //MORPHO_CN10_16
    pinMode(PA_11, INPUT_PULLDOWN); //MORPHO_CN10_14
    pinMode(PA_12, INPUT_PULLDOWN); //MORPHO_CN10_12
    pinMode(PC_5, INPUT_PULLDOWN); //MORPHO_CN10_6
    pinMode(PC_6, INPUT_PULLDOWN); //MORPHO_CN10_4
    pinMode(PC_8, INPUT_PULLDOWN); //MORPHO_CN10_2

    MORPHO_CN7
    PA13(3) Checar cuál es la nota
    PA (3) ídem
    pinMode(PC10, INPUT_PULLDOWN);
    pinMode(PD12, INPUT_PULLDOWN);
    pinMode(PA15, INPUT_PULLDOWN);
    pinMode(PB7, INPUT_PULLDOWN);
    pinMode(PC13, INPUT_PULLDOWN);
    pinMode(PC14, INPUT_PULLDOWN);
    pinMode(PC15, INPUT_PULLDOWN);
    pinMode(PH0, INPUT_PULLDOWN);
    pinMode(PH1, INPUT_PULLDOWN);
    pinMode(PC2, INPUT_PULLDOWN);
    pinMode(PC3, INPUT_PULLDOWN);
    */
#endif
}
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

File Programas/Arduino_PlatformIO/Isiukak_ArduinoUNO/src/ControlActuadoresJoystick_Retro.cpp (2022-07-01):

/*****************************************************************************

La configuración general del sistema puede consultarse en README.md

******************************************************************************/

#include "Seguridad.hpp"
#include "Testing.hpp"

//****************************** Variables de programa *************************//
/*int pinJoystickY = A0;
int pinJoystickX = A1;
int pinActFreno  = A2;
int pinActAcel   = A3;

int pinFijarPosicionFreno = 10; //10
int pinSubirPalanca = A5; //A5
int pinBajarPalanca = 11; //11
int pinModoCarretera = A4; //A4

int pinBotonParoEmergencia = 9;

*/

//Variables para la medición del periodo del sistema.
long tiempoAnterior = 0, tiempoActual = 0;

boolean actualizacionExitosa = false;
//******************************************************************************//


void Control(int Joystick_X, int Joystick_Y,
                uint8_t ActuadorFreno_EstaInhibido,
                uint8_t ActuadorAcelerador_EstaInhibido,
                TiposControlVolante tipoControlVolante)
{
/*!
 *****************************************************************************************/

    // *************  *************** //

    ControlarPedales(Joystick_Y, FijarPosicionFreno, Joystick_comportamientoDirecto,
                     ActuadorFreno_EstaInhibido, ActuadorAcelerador_EstaInhibido);


    ControlarVolante(Joystick_X, tipoControlVolante);


    ControlPalanca(ActuadorFreno_Posicion);
}

void configurarPines()
{
    analogReference(EXTERNAL);
    //DEFAULT: the default analog reference of 5 volts (on 5V Arduino boards) or 3.3 volts (on 3.3V Arduino boards)
    //EXTERNAL: the voltage applied to the AREF pin (0 to 5V only).

    pinMode(pinBotonParoEmergencia, INPUT_PULLUP); //Configurar el pin por defecto en alto.

    pinMode(pin5VVirtual, OUTPUT);
    pinMode(pinGNDVirtual, OUTPUT);

    pinMode(pinFijarPosicionFreno, INPUT);
    pinMode(pinSubirPalanca, INPUT);
    pinMode(pinBajarPalanca, INPUT);
    pinMode(pinModoCarretera, INPUT);

    pinMode(pinOutput_PalancaBajar, OUTPUT);
    pinMode(pinOutput_PalancaSubir, OUTPUT);
    digitalWrite(pinOutput_PalancaBajar, LOW);
    digitalWrite(pinOutput_PalancaSubir, LOW);

    //pinMode(pin_encendido, INPUT_PULLUP); //Por defecto en alto
}

void desplegarInfoArranque()
{
    Serial.print("**Modo Operación Joystick: ");

    if(Joystick_comportamientoDirecto)
    {
        Serial.println("Directo. **");
    }
    else
    {
        Serial.println("Inverso. **");
    }

#if FRENO_ACTIVADO //Usar ! para negar la constante no funciona como con una variable normal.
    Serial.println("**El Freno está Activado.**");
#else
    Serial.println("**¡EL FRENO NO ESTÁ ACTIVADO!**");
#endif

#if ACELERADOR_ACTIVADO
    Serial.println("**El Acelerador está Activado.**");
#else
    Serial.println("**¡EL ACELERADOR NO ESTÁ ACTIVADO!**");
#endif

#if EMBEDDED_TESTING
    Serial.println("**EMBEDDED TESTING**");
#endif

#if TESTING_MODE
    calculate_IterationsPerActuator(periodoDeseado);
    Serial.println("**TESTING MODE**");
#endif

#if JOYSTICK_VIRTUAL
    Serial.println("**JOYSTICK VIRTUAL**");
#endif

#if ENTRADAS_VIRTUALES
    Serial.println("**ENTRADAS VIRTUALES**");
#endif


#if DEBUG_CONTROL_VOLANTE_UMBRALES
    //Serial.print("JoyIzq_Medio: "); Serial.println(joyIzquierdaMedio);
    //Serial.print("JoyDer_Medio: "); Serial.println(joyDerechaMedio);

    //Serial.print("JoyIzq_2/3: "); Serial.println(joyIzqDosTer);
    //Serial.print("JoyDer_2/3: "); Serial.println(joyDerDosTer);


    Serial.println("Corroborando valores de control por segmentos para Joystick y Actuación del volante");
    Serial.print("porcentControlPuente_Seg1:  ");
    Serial.println(porcentControlPuente_Seg1);//Segmento1
    Serial.print("ControlVolante_IzqSeg1: ");
    Serial.println(ControlVolante_IzqSeg1);
    Serial.print("ControlVolante_DerSeg1");
    Serial.println(ControlVolante_DerSeg1);

    Serial.print("joy_percentSegmento1: ");
    Serial.println(joy_percentSegmento1);
    Serial.print("joyIzq_Segmento1: ");
    Serial.println(joyIzq_Segmento1);
    Serial.print("joyDer_Segmento1: ");
    Serial.println(joyDer_Segmento1);
    delay(2000);
#endif

    Serial.print("**Periodo verificación: "); Serial.println(periodoVerificacion);
    Serial.print("**Periodo Deseado: "); Serial.println(periodoDeseado);
    Serial.print("**Cantidad de iteraciones para verificación: "); Serial.println(cantIteracionesParaVerificacion);
}

void displayInfoTime()
{
#if INFO_TIME
    long diferencia = tiempoActual - tiempoAnterior;
    Serial.print(",\tT:"); Serial.print(diferencia);
#endif
    Serial.println(" ");
    tiempoAnterior = tiempoActual;
}

void displayInfo()
{
    desplegarInfoJoystick();
    desplegarInfoBotones();

    desplegarInfoPedales();

    desplegarInfoVolante();
    desplegarInfoPalanca(ActuadorFreno_Posicion);

    desplegarInfoEstadoSistema();
}


void setup()
{
    /// TODO: Portar a Infineon.

    //Serial.begin(38400);
    Serial.begin(115200);
    Serial.println("Comunicación Serial Iniciada.");
    //smcSerial.begin(19200);
    smcSerial.begin(9600); // Se probó con 19200 y funciona.
    /// TODO: Investigar si menor velocidad Serial es menos exigente para el micro.

    configurarPines();

    Pots_verificacion_activarVoltajeVirtual();

    Feedback_fillBuffer();

    // Verificación de seguridad al arranque.
    /*
    erroresArranque = verificacionSeguridad_Boot();
    if(erroresArranque)
    {
        Serial.println("**Se detectaron errores durante el arranque.**");
    }
    while(erroresArranque)
    {
        erroresArranque = verificacionSeguridad_Boot();
        aplicarRutinasSeguridad_boot(Joystick_Centrado, EstadoDelSistema);
        feedbackOnly();
    }
    */

#if VOLANTE_ACTIVADO
    volante_Desinhibir();
#endif

    tiempoAnterior = millis();

    desplegarInfoArranque();
}
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

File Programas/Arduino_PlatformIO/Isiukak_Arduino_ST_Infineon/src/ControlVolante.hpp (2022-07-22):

#ifndef CONTROLVOLANTE
#define CONTROLVOLANTE

//**************** Variables y librerias para control de direccion ********************//
/* En esta sección están las variables y funciones para controlar el volante. */

#if ENCODER_ACTIVADO
    //#include <EEPROM.h> //Para almacenar valores en memoria no volatil.
    //#include "LecturaEncoder.hpp" //->//#include "Seguridad.hpp"
#endif
//#include "DigitalFilter.hpp"
#include "LecturaFeedback.hpp"
#include "ControlPedales.hpp" //->//#include "LecturaJoystick.hpp"
                              //->//#include "DriversMotores.hpp"


int CtrlVolante_valMin = 200; //Por debajo de este valor el motor no se mueve, aún si ya estaba en movimiento.
int CtrlVolante_valMax = 3200;
//int controlVolanteMaximo = 2400;

//*****************************Variables configuración**************************
#if ENCODER_ACTIVADO
/// Variables para control de Posición
//El volante puede girar una vuelta y 3/4 aproximadamente hacia izquierda y derecha.
//Su centro es en: 0 vueltas, 0°. 360+270 = 630. Sin embargo eso debe ser
//convertido al angulo del encoder.

//Cálculo de la relación entre las vueltas del volante y las vueltas del motor.
int dientesEje = 20;   //Num de dientes del sprocket del volante.
int dientesMotor = 14; //Num de dientes del sprocket del motor.
float relacionSprockets = (float)dientesEje / dientesMotor;

float setPointGrados = 180.0 / relacionSprockets;
//float ajusteGrados180 = 0.0;

//Rango de giro del volante a izquierda y derecha.
//El máximo aproximado es 1 y 3/4 de vuelta (360 + 270 = 630), pero se redujo ligeramente para evitar
//llevarla al límite.
int gradosVolanteIzq = -610 + setPointGrados;
int gradosVolanteDer = 610 + setPointGrados;
int anguloSeguridadVueltaIzq = 50 ;
int anguloSeguridadVueltaDer = 50;
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

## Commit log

2021-04-19 Agregado Modulo_Control
    [ActivadorLimitSwitch.FCStd, ActivadorLimitSwitch.stl, ActivadorLimitSwitch_v2.stl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]
2021-05-04 Programa actualizado y con niveles de emergencia implementados
    [Configuración Encoder.txt, DiagramaGeneral.fzz]
2021-08-26 Actualización 21-08-25
    [ActivadorLimitSwitch.FCStd, ActivadorLimitSwitch.stl, ActivadorLimitSwitch_v2.stl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]
2021-09-28 Versión del 2021 09 28
    [ActivadorLimitSwitch.FCStd, ActivadorLimitSwitch_v4.stl, AngularSoporte_Motor.fcstd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]
2021-09-30 Versión 2021-09-30
    [ActivadorLimitSwitch.FCStd, ActivadorLimitSwitch_v4.stl, AngularSoporte_Motor.fcstd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]
2021-11-08 Mejoras 21-11-05
    [ActivadorLimitSwitch.FCStd, ActivadorLimitSwitch_v4.stl, AngularSoporte_Motor.fcstd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]
2021-11-27 Versión 21/11/26 para repositorio público
    [Joystick_Circuito_Fritzing.fzz]
2022-02-27 Se agregó el código de Arduino para el STM32 F40
2022-03-31 Release de marzo 2022 del Isiukak
    [Configuración.txt]
2022-04-30 Versión abril con lectura de drivers
2022-05-05 Corrección de la lectura de los drivers de Pololu
2022-07-01 Soporte para tarjet ST Nucleo F401RE e Infineon Relax Kit XMC4700
2022-07-17 Actualización de mensajes en TESTING_EMBEDDED
2022-07-21 Mejoras al monitor serial corrigiendo el minValue del JY y cuestiones estéticas
    [Config.hpp, ControlPedales.hpp, ControlVolante.hpp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]
2022-07-22 Actualizando para merge
2022-07-22 Agregadas las reglas udev de tarjetas ST
2022-07-26 Se agregó opción en el menú para guardar los valores mínimo y máximo del Joystick, Acelerador y Freno
2022-07-26 Push para pull
2022-08-26 Se agregó lectura del sensor de temperatura del ST NUCLEO F401RE
2022-08-30 Se reconfiguraron los directorios para build Release y build Debug. También se agregaron líneas al gitignores para no subir esos directorios al repositorio
